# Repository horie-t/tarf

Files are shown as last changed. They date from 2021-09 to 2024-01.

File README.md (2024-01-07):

# Tarf

マイクロ・マウスを制作するプロジェクトです。

https://user-images.githubusercontent.com/10256609/150635355-fdfd84de-0ae6-4175-8a13-437b662bb9f7.mp4

Tarfは以下の特徴を持ちます。

* 筐体は3Dプリンタで制作
* 制御には、Wio Terminalを使用
* 制御用のFrimwareは、Rustで実装

## Rust開発環境のセットアップ

Ubuntu上で開発しています。

開発に必須のパッケージをインストールします。

```bash
sudo apt install build-essential git
```

Rustのツール・チェーンをインストールします。

[rustup](https://rustup.rs/) の指示に従ってインストールします。

クロスビルド用のツール・チェーンをインストールします。

```bash
rustup target add thumbv7em-none-eabihf
```

Wio Terminal用に必要なパッケージをインストールします。

```bash
sudo apt install libusb-1.0-0-dev libsdl2-dev libssl-dev
```

シリアルデバイスの読み書き権限の設定

```bash
sudo adduser $USER dialout
```

上記で、Wio Terminalにプログラムの書き込みができない場合は以下のファイルを作成します。

/etc/udev/rules.d/99-seeed-boards.rules
```
ATTRS{idVendor}=="2886", ENV{ID_MM_DEVICE_IGNORE}="1"
SUBSYSTEM=="usb", ATTRS{idVendor}=="2886", MODE="0666"
SUBSYSTEM=="tty", ATTRS{idVendor}=="2886", MODE="0666"
```

作成後、以下のコマンドを実行します。

```bash
sudo udevadm control --reload-rules
```

## 開発記録

Firmware

| ステップ | 内容 |
| --- | --- |
| 1 | [内蔵LEDでLチカ](./firmware/l-chika)をしてみる。 |
| 2 | ブレッドボードに接続して、[外部のLEDでLチカ](./firmware/l-chika-external)してみる。 | 
| 3 | L6470モータドライバを使って、[ステッピングモータを駆動](./firmware/stepper-motor)させてみる。|
| 4 | L6470モータドライバを使って、[ステッピングモータをステップ数指定で駆動](./firmware/stepper-motor-count)させてみる。|
| 5 | 外部の[スイッチからの割込み](./firmware/interrupt-external)を受け付ける。 |
| 6 | [ステッピングモータの動作完了を割込みで処理する](./firmware/stepper-motor-interrupt)。 |
| 7 | A4988モータドライバを使って、[ステッピングモータを駆動](./firmware/stepper-motor-a4988)させてみる。 |
| 8 | [3つのステッピングモータを駆動](./firmware/stepper-motor-a4988-3motor)させてみる。 |
| 9 | TimerContorllerの割込みを使って[3つのステッピングモータを別々の回転数で駆動](./firmware/stepper-motor-a4988-timer)させてみる。 |
| 10 | [試作1号機で往復運動](./firmware/reciprocating-motion)をさせてみる。 |
| 11 | [往復運動をタイマー割込み](./firmware/reciprocating-timer)でさせてみる。 |
| 12 | [三角形の軌跡](./firmware/triangle-motion)を描くように移動させる。 |
| 13 | 段々と速度を上げる[加速運動](./firmware/accelaration)をさせる。 |
| 14 | [TOF 距離センサ](./firmware/tof-sensor/)を接続する。 |
| 15 | [LCDに文字](./firmware/lcd-display/)を表示する。 |
| 16 | [TOF 距離センサを6つ](./firmware/tof-sensor-hub-6/)接続する。 |
| 17 | [TOF 距離センサで連続測定モード](./firmware/tof-sensor-interrupt/)で測定する。 |
| 18 | [2マスの直線だけの迷路](./firmware/straight-line-maze/)を走行する。 |
| 19 | [L字型迷路](./firmware/l-shaped-maze/)をデッド・レコニングで走行する。 |
| 20 | [長い直線迷路](./firmware/long-straight-maze/)を補正しながら走行する。 |
| 21 | [スタート位置で向きと位置を調整](./firmware/adjust-position/)してから走行する。 |
| 22 | [4マスの迷路](./firmware/quad-cell-maze/)を走行する。 |
| 23 | 9マスの[渦巻き状の迷路](./firmware/spiral-maze/)を走行する。 |
| 23 | 9マスの[迷路を描画](./firmware/map-display/)してみる。 |
| 23 | 9マスの渦巻き状の迷路を[現在地を表示](./firmware/current-pose/)しながら走行する。 |
| 24 | 9マスの渦巻き状の迷路を[側面の壁を表示](./firmware/wall-state/)しながら走行する。 |
| 25 | [BNO055 9軸センサ](./firmware/9axis-sensor/)を接続する。 |
| 26 | [UARTにHello, worldを出力](./firmware/uart/)する。 |
| 25 | [9軸センサをI2Cハブ](./firmware/9axis-sensor-hub/)に接続する。 |
| *** | 以降、設計見直し |
| 26 | [内蔵LEDでLチカ(その3)](./firmware/l-chika-3)をしてみる。 |

Body

| ステップ | 内容 |
| --- | --- |
| 1 | [ステッピングモータを固定](./cad/core1_3_motor) |
| 2 | [ステッピングモータを固定の向きを変更](./cad/core1_3_motor2) |
| 3 | [ステッピングモータとWio Terminal部分との接続部を追加](./cad/core1_3_motor3) |
| 4 | [Wio Terminalとバッテリーの収納部](./cad/core2) |
| 5 | [オムニホイールのハブを作成](./cad/wheel_hub) |
| 6 | [TOF距離センサを搭載](./cad/core1_motor_sensor_4) |
| 7 | [Wio Terminalとバッテリーの収納部にI2Cハブを搭載](./cad/core2_3) |
| *** | 以降大幅な設計変更 |
| 8 | [TOF距離センサの位置を変更](./cad/core1_motor_sensor_5/) |
| 9 | [Wio Terminalとバッテリーの格納部の下部の長さ調整](./cad/core2_5/) |

curcuit
| ステップ | 内容 |
| --- | --- |
| 1 | [回路図](./circuit/universal_board_both.svg)  |

## 参考情報

* embedded-halクレートの[RustDoc](https://docs.rs/embedded-hal/0.2.6/embedded_hal/)
* ATSAMDマイコンのRustクレートの[リポジトリ](https://github.com/atsamd-rs/atsamd)  
  Wio Terminalのクレートもこの中
* atsamd51pのRustクレートの[RustDoc](https://docs.rs/atsamd51p/0.9.0/atsamd51p/)
* wio_terminalクレートの[RustDoc](https://docs.rs/wio_terminal/0.3.0/wio_terminal/)

* VL53L0Xの[使い方](./docs/VL53L0X.md)

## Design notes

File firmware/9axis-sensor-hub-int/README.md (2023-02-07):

# 9軸センサーをI2Cハブ経由で接続し、割込みで測定する

2023-02-07: 上手く割込みが動作しない

## 使用パーツ

* [Wio Terminal](https://www.switch-science.com/catalog/6360/)
* [Wio Terminal バッテリーベース](https://www.switch-science.com/catalog/6816/)
* [ＢＮＯ０５５使用　９軸センサーフュージョンモジュールキット](https://akizukidenshi.com/catalog/g/gK-16996/)
* [Grove 8チャンネルI2Cマルチプレクサ/I2Cハブ(TCA9548A)](https://eleshop.jp/shop/g/gK2C313/)
* [USBシリアル変換モジュール(通販コード:M-11007)](https://akizukidenshi.com/catalog/g/gM-11007/)

## 測定値をパソコンで確認

Linuxの場合:

minicomをインストールして、以下のコマンドを実行します。

```bash
minicom -D /dev/ttyUSB0
```

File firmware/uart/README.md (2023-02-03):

# 9軸センサー

## 使用パーツ

* [Wio Terminal](https://www.switch-science.com/catalog/6360/)
* [USBシリアル変換モジュール(通販コード:M-11007)](https://akizukidenshi.com/catalog/g/gM-11007/)

## 測定値をパソコンで確認

Linuxの場合:

minicomをインストールして、以下のコマンドを実行します。

```bash
minicom -D /dev/ttyUSB0
```

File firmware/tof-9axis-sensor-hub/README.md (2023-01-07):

# 9軸センサー

## 使用パーツ

* [Wio Terminal](https://www.switch-science.com/catalog/6360/)
* [Wio Terminal バッテリーベース](https://www.switch-science.com/catalog/6816/)
* [ＢＮＯ０５５使用　９軸センサーフュージョンモジュールキット](https://akizukidenshi.com/catalog/g/gK-16996/)
* [USBシリアル変換モジュール(通販コード:M-11007)](https://akizukidenshi.com/catalog/g/gM-11007/)

## ブレッドボードで接続する場合の接続図

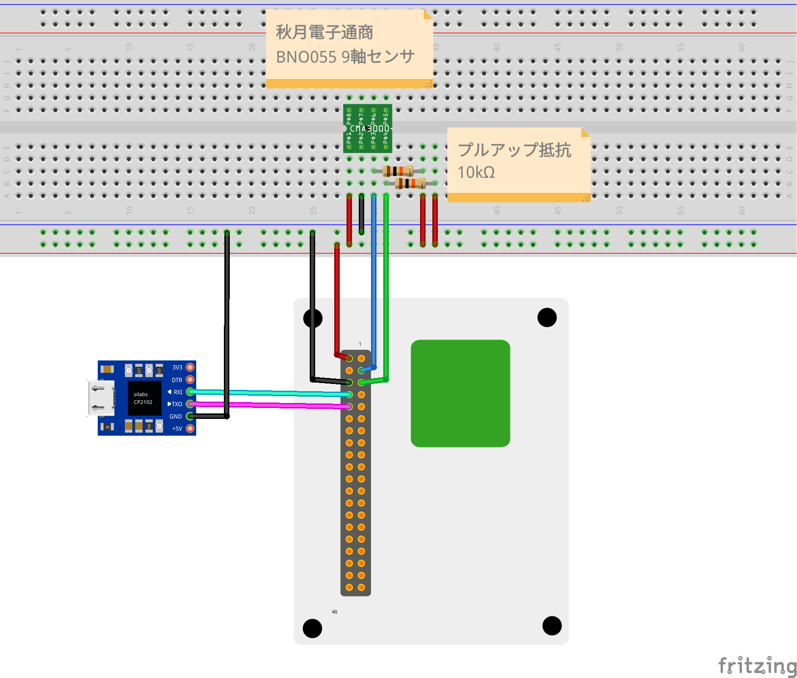
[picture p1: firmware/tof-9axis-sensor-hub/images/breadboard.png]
Breadboad


## 測定値をパソコンで確認

Linuxの場合:

minicomをインストールして、以下のコマンドを実行します。

```bash
minicom -D /dev/ttyUSB0
```

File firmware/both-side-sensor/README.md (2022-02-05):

# 両側のセンサの測定値で走行する

両側のセンサの値を使って走行する。できるだけ直進性を上げるのが目標。

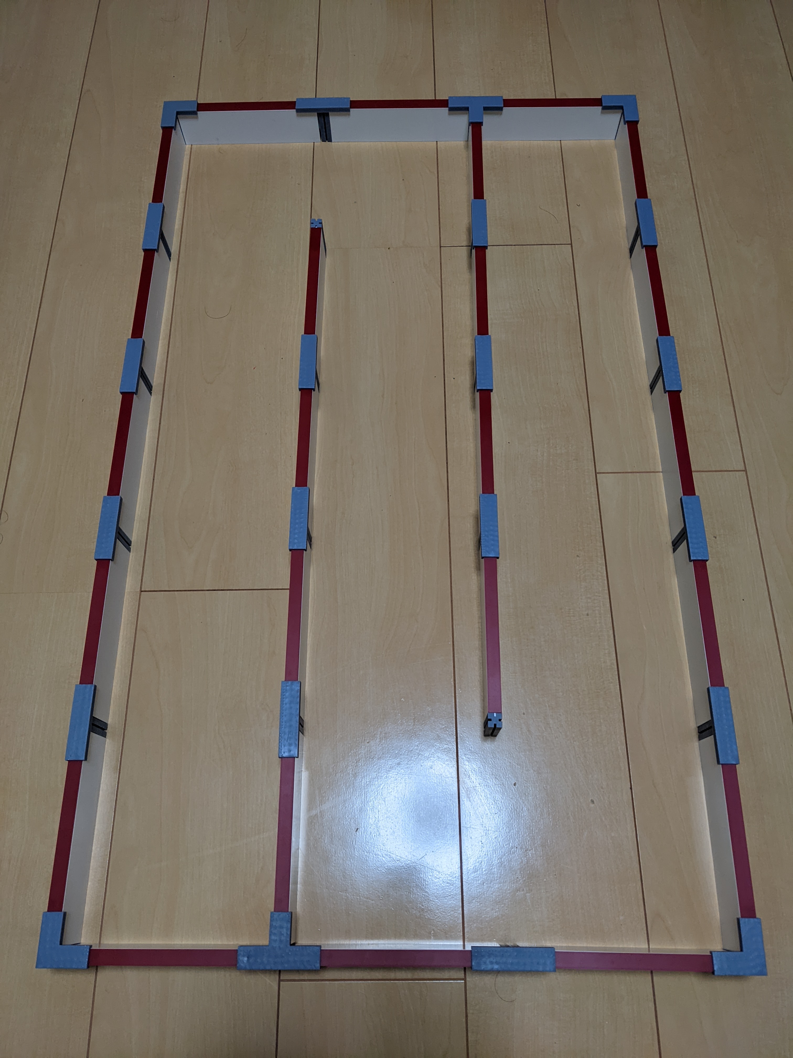
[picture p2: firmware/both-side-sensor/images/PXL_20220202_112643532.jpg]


## 使用パーツ

* [Wio Terminal](https://www.switch-science.com/catalog/6360/)
* [Wio Terminal バッテリーベース](https://www.switch-science.com/catalog/6816/)
* [バイポーラ・ステッピングモータ](https://jp.misumi-ec.com/vona2/detail/221005433134/?HissuCode=SS2421-5041)
* [A4988 ステッピングモータ・ドライバ・モジュール](https://amzn.to/39Z4EZu)
* [ToF レーザーモジュール(VL53L0X)](https://www.amazon.co.jp/gp/product/B08NDN4L9H/)
* [Grove 8チャンネルI2Cマルチプレクサ/I2Cハブ(TCA9548A)](https://eleshop.jp/shop/g/gK2C313/)
* [LiPoバッテリー](https://amzn.to/3DF7PCH)
* [クラシックサイズマイクロマウス迷路用 壁 (プラスチック)](https://www.rt-shop.jp/index.php?main_page=product_info&products_id=3745)

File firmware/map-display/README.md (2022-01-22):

# 地図描画

地図、ルートと自車位置を描画します。



## 使用パーツ

* [Wio Terminal](https://www.switch-science.com/catalog/6360/)

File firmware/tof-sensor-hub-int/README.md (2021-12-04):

# TOFセンサー

連続測定モードで測定

## 使用パーツ

* [Wio Terminal](https://www.switch-science.com/catalog/6360/)
* [Wio Terminal バッテリーベース](https://www.switch-science.com/catalog/6816/)
* [ToF レーザーモジュール(VL53L0X)](https://www.amazon.co.jp/gp/product/B08NDN4L9H/)
* [USBシリアル変換モジュール(通販コード:M-11007)](https://akizukidenshi.com/catalog/g/gM-11007/)

## ブレッドボードで接続する場合の接続図

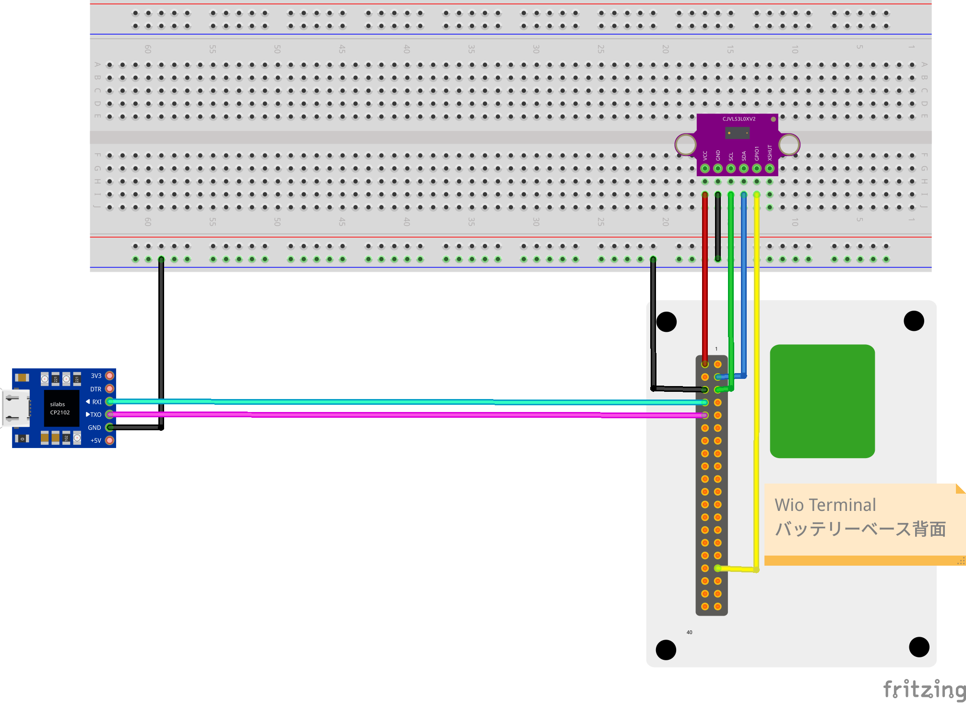
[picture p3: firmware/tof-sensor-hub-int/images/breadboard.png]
Breadboad


## 測定値をパソコンで確認

Linuxの場合:

minicomをインストールして、以下のコマンドを実行します。

```bash
minicom -D /dev/ttyUSB0
```

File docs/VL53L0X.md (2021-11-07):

# VL53L0Xの簡単な説明

## はじめに

VL53L0Xはレーザー光を利用したTOF型距離センサです。

最大測定距離は以下の通り。

| Target reflectance level(full FOV) | Conditions | Indoor(2)  | Outdoor overcast (2) |
| --- | --- | --- | --- |
| White target (88%) | Typical | 200cm+ (1) | 80cm |
| | Minimum | 120cm | 60cm |
| Grey target (17%) | Typical | 80cm | 50cm |
| | Minimum | 70cm | 40cm |

(VL53L0X Datasheet P.26より)

ホストとはI2Cで接続されます。I2Cバスの最大速度は400kbpsです。レジスタの仕様は公開されていない。

## 距離の測定

測定方法は以下の2つの方法です。

* ポーリングモード
* 割込みモード: 値が利用可能になると割込みピン(GPIO1)がホストに割込みを送信します。

## 測定シーケンス

ポーリングモードで測定する場合はAPI呼び出し後、timing buget(デフォルトは33msec) の時間以内で測定します。

## 測定プロファイル

| Range profile | Range timing budget | Typical performance | Typical application |
| --- | --- | --- | --- |
| Default mode  | 30 ms | 1.2 m, accuracy omit | Standard |
| High accuracy | 200 ms | 1.2 m, accuracy < +/- 3 % | Precise measurement |
| Long range | 33 ms | 2 m, accuracy omit | Long ranging, only for dark conditions  (no IR) |
| High speed | 20 ms | 1.2 m, accuracy +/- 5 % | High speed where accuracy is not priority |

(VL53L0X Datasheet P.28より)

timing budgetは、最小 20 ms, 最大 1000 ms。

## vl53l0xクレートの使用方法

Cargo.tomlの設定は [creates.io](https://crates.io/crates/vl53l0x) を参照。

**【インスタンスの生成】**
VL53L0x::new(i2c)

**【単発での測定】**

1. read_range_single_millimeters_blocking()

**【割込みでの連続測定】**

1. start_continuous(timing budgetのミリ秒)
2. 割込み発生
3. read_range_continuous_millimeters_blocking() もしくは read_range_mm()
4. 2, 3の繰り返し
5. (測定停止の場合)stop_continuous()

**【timing budget】**

get_measurement_timing_budget(ミリ秒)
set_measurement_timing_budget(ミリ秒)

使用例

* ポーリングモードの[例](../firmware/tof-sensor/src/main.rs)

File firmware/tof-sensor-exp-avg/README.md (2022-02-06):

# TOFセンサー

連続測定モードで測定し、指数平滑平均で表示する。

壁が直角



| 距離(mm) | センサ0 | センサ1 | センサ2 | センサ3 | センサ4 | センサ5 |
| --- | --- | --- | --- | --- | --- | --- |
| 10 | 28 | 17 | 14 | 22 | 20 | 38 |
| 20 | 33 | 24 | 23 | 24 | 25 | 41 |
| 30 | 49 | 37 | 37 | 37 | 36 | 53 |
| 40 | 59 | 47 | 48 | 42 | 49 | 62 |
| 50 | 68 | 56 | 55 | 51 | 55 | 68 |
| 60 | 76 | 66 | 65 | 59 | 67 | 80 |
| 70 | 88 | 77 | 74 | 73 | 76 | 92 |
| 80 | 98 | 88 | 87 | 82 | 87 | 102 |
| 90 | 109 | 97 | 96 | 93 | 96 | 112 |
| 100 | 118 | 106 | 105 | 104 | 105 | 123 |
| 120 | 138 | 130 | 129 | 122 | 127 | 141 |
| 140 | 161 | 151 | 149 | 146 | 148 | 164 |
| 160 | 179 | 169 | 170 | 161 | 168 | 184 |
| 180 | 198 | 187 | 189 | 186 | 186 | 202 |
| 200 | 217 | 208 | 209 | 206 | 205 | 220 |

壁が30°傾斜



| 距離(mm) | センサ0 | センサ1 | センサ2 | センサ3 | センサ4 | センサ5 |
| --- | --- | --- | --- | --- | --- | --- |
| 10 | 35 | 35 | 29 | 32 | 31 | 45 |
| 20 | 45 | 39 | 35 | 38 | 37 | 51 |
| 30 | 57 | 49 | 49 | 44 | 51 | 57 |
| 40 | 63 | 56 | 52 | 53 | 57 | 63 |
| 50 | 74 | 68 | 65 | 64 | 66 | 75 |
| 60 | 85 | 80 | 76 | 75 | 76 | 86 |
| 70 | 96 | 90 | 86 | 84 | 87 | 97 |
| 80 | 107 | 101 | 96 | 96 | 98 | 109 |
| 90 | 118 | 112 | 107 | 108 | 107 | 119 |
| 100 | 128 | 123 | 118 | 119 | 117 | 131 |
| 120 | 148 | 142 | 139 | 140 | 138 | 153 |
| 140 | 167 | 162 | 158 | 161 | 157 | 172 |
| 160 | 187 | 179 | 178 | 181 | 176 | 191 |
| 180 | 206 | 197 | 196 | 200 | 196 | 212 |
| 200 | 223 | 215 | 214 | 219 | 215 | 231 |

## 使用パーツ

* [Wio Terminal](https://www.switch-science.com/catalog/6360/)
* [Wio Terminal バッテリーベース](https://www.switch-science.com/catalog/6816/)
* [ToF レーザーモジュール(VL53L0X)](https://www.amazon.co.jp/gp/product/B08NDN4L9H/)
* [Grove 8チャンネルI2Cマルチプレクサ/I2Cハブ(TCA9548A)](https://eleshop.jp/shop/g/gK2C313/)
* [USBシリアル変換モジュール(通販コード:M-11007)](https://akizukidenshi.com/catalog/g/gM-11007/)

## ブレッドボードで接続する場合の接続図

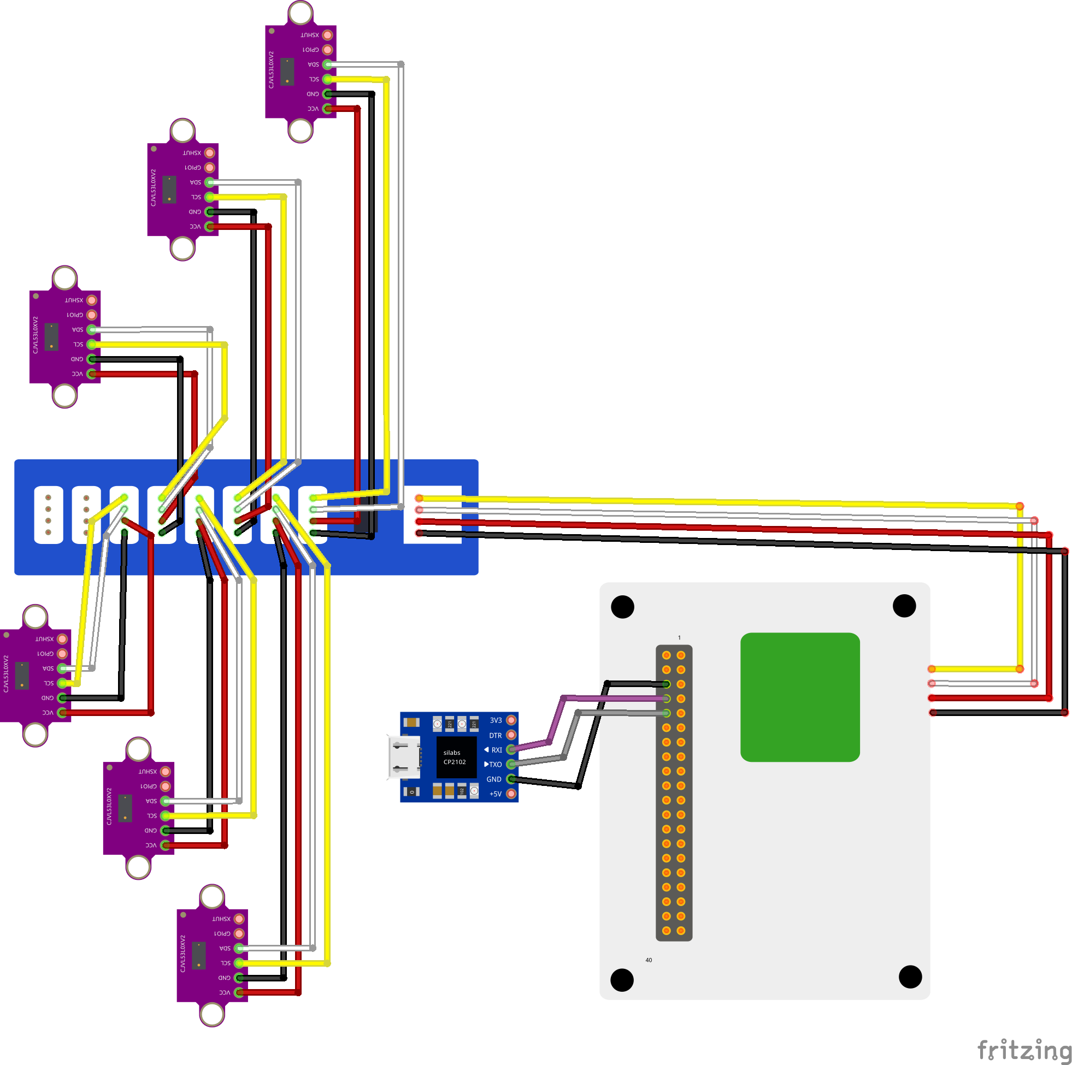
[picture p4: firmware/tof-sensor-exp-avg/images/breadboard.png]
Breadboad


## 測定値をパソコンで確認

Linuxの場合:

minicomをインストールして、以下のコマンドを実行します。

```bash
minicom -D /dev/ttyUSB0
```

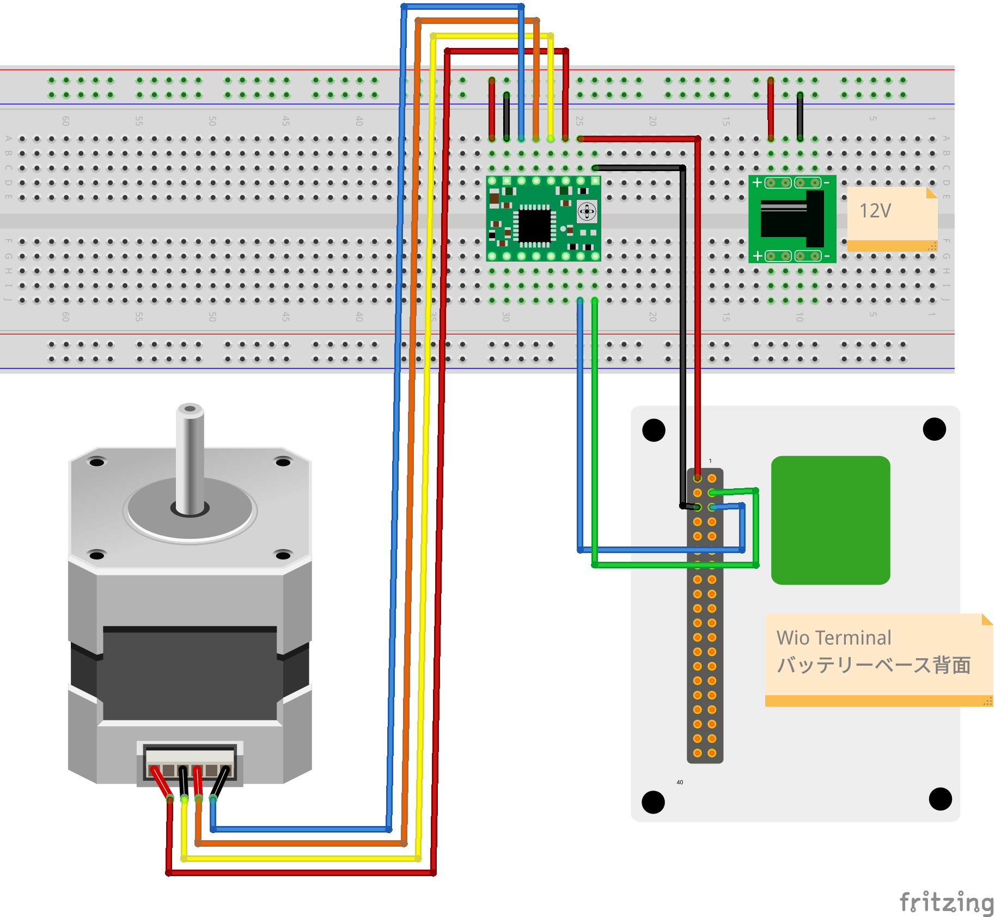
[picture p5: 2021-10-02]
firmware/stepper-motor-a4988/images/stepper_motor_breadboard.png

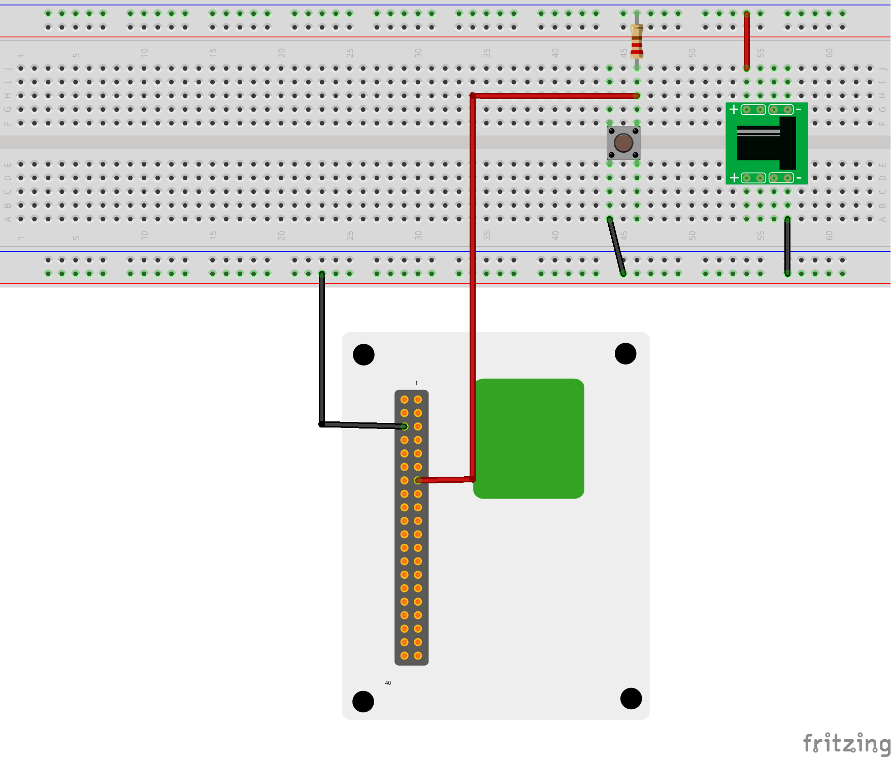
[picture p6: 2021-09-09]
firmware/interrupt-external/images/button_external.png

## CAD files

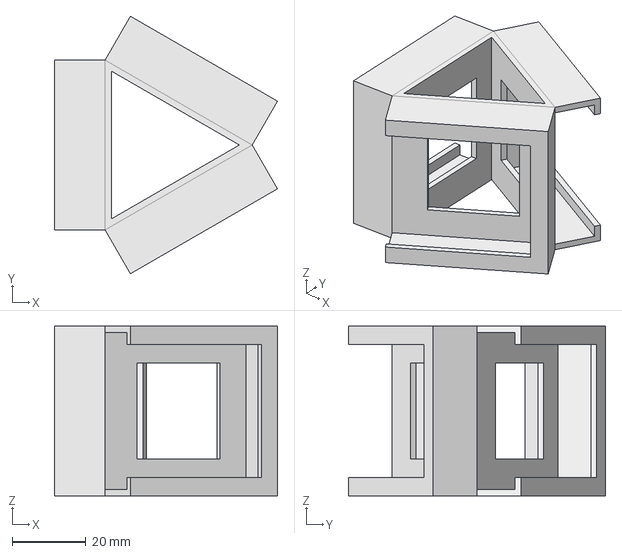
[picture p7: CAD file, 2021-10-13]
cad/core1_3_motor/core1_3_motor.FCStd
60.4 x 69.7 x 46.0 mm

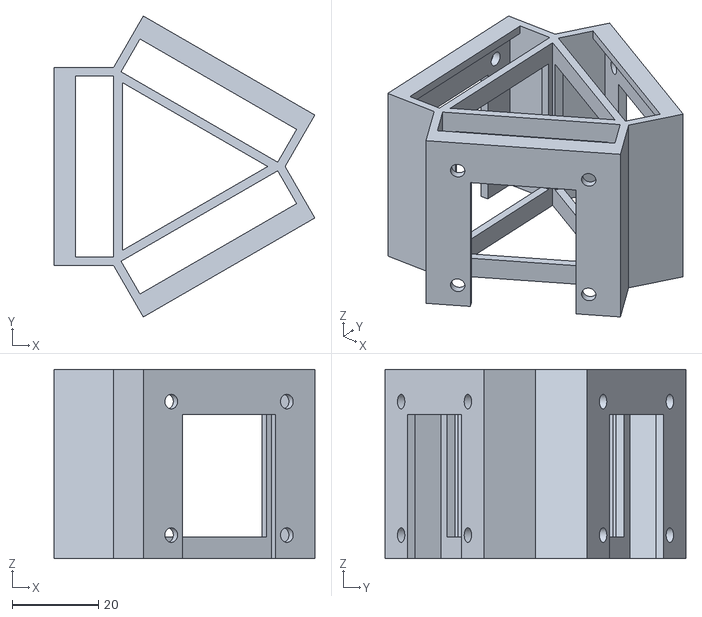
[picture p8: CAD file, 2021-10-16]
cad/core1_3_motor_2/core1_3_motor_2-Body.stl
60.5 x 69.9 x 44.0

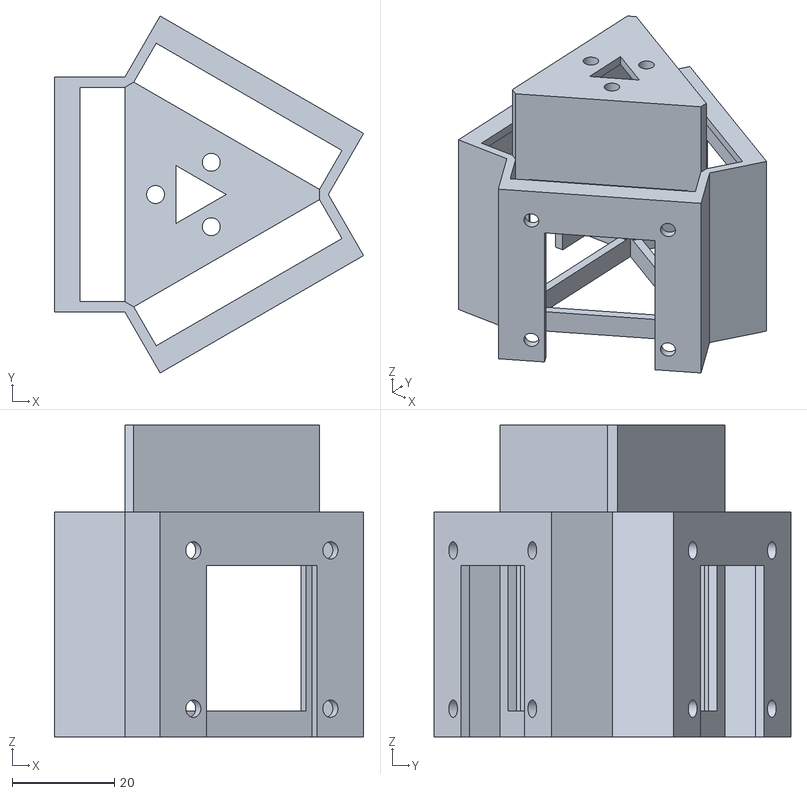
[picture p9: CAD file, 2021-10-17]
cad/core1_3_motor_3/core1_3_motor_3-Body.stl
60.5 x 69.9 x 61.0

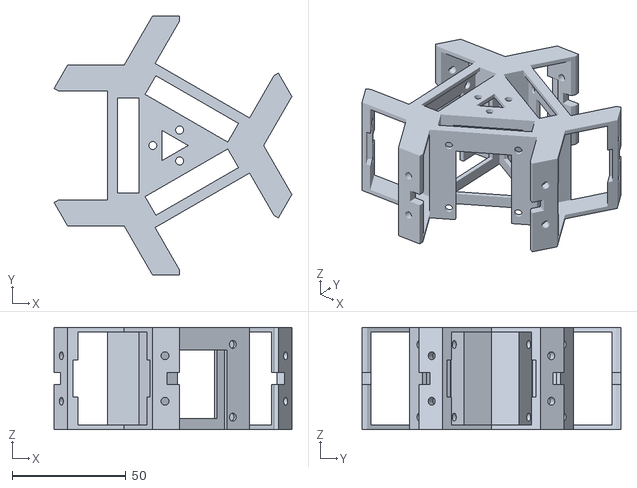
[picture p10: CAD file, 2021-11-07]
cad/core1_motor_sensor/core1_motor_sensor-Body.stl
104.7 x 114.0 x 45.0

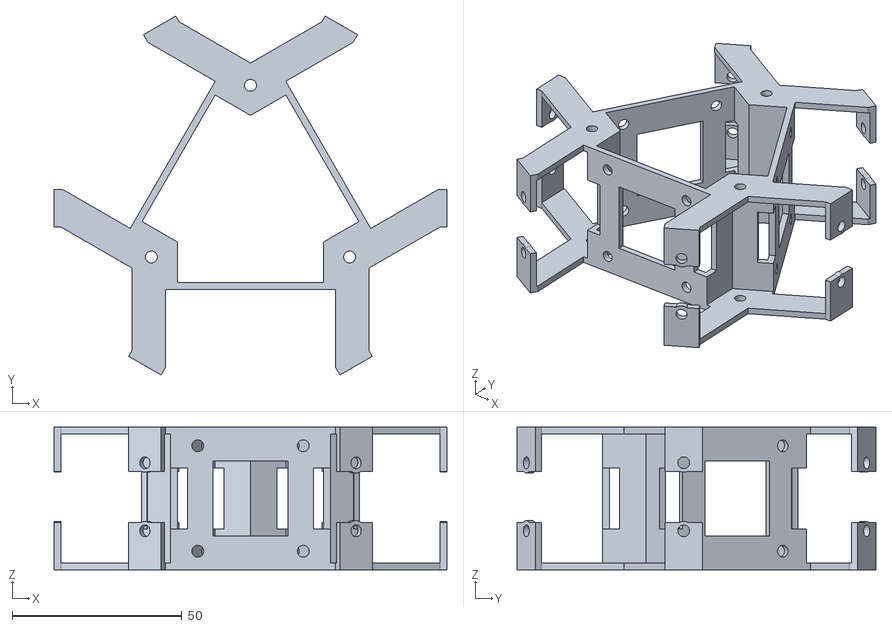
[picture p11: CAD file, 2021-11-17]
cad/core1_motor_sensor_2/core1_motor_sensor_2-Body.stl
115.6 x 105.6 x 42.0

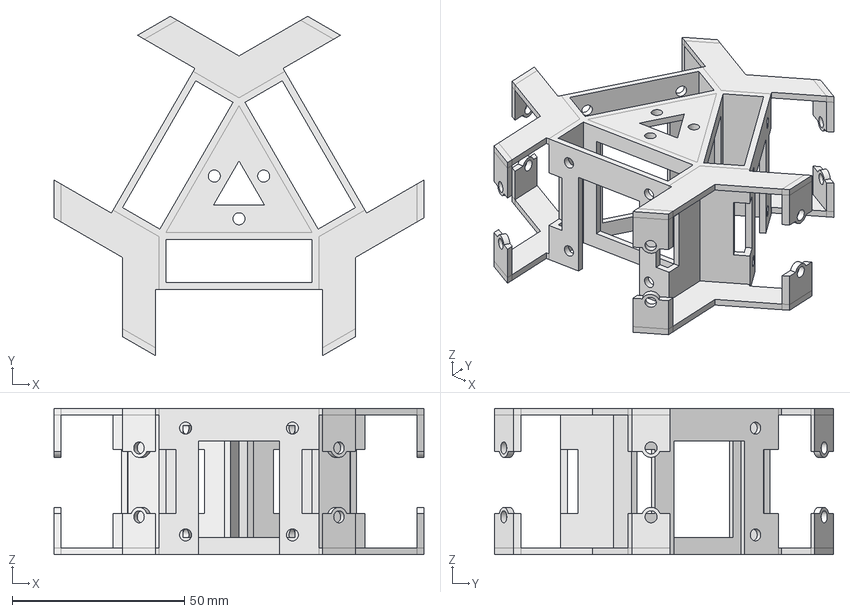
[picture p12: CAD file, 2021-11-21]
cad/core1_motor_sensor_4/core1_motor_sensor_4.FCStd
107.4 x 98.5 x 42.5 mm

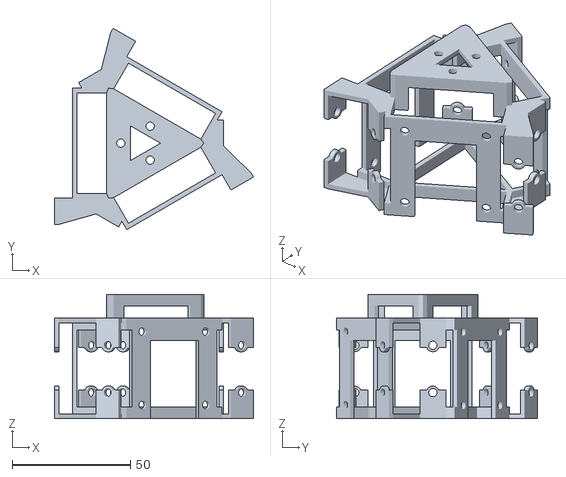
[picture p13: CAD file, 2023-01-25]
cad/core1_motor_sensor_5/core1_motor_sensor_5-Body.stl
84.1 x 85.1 x 52.5

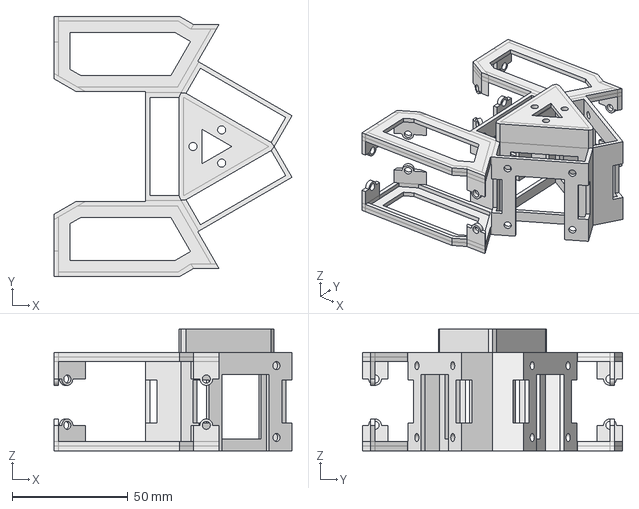
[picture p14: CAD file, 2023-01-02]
cad/core1_motor_tof_9axis/core1_motor_tof_9axis.FCStd
102.8 x 112.5 x 52.5 mm

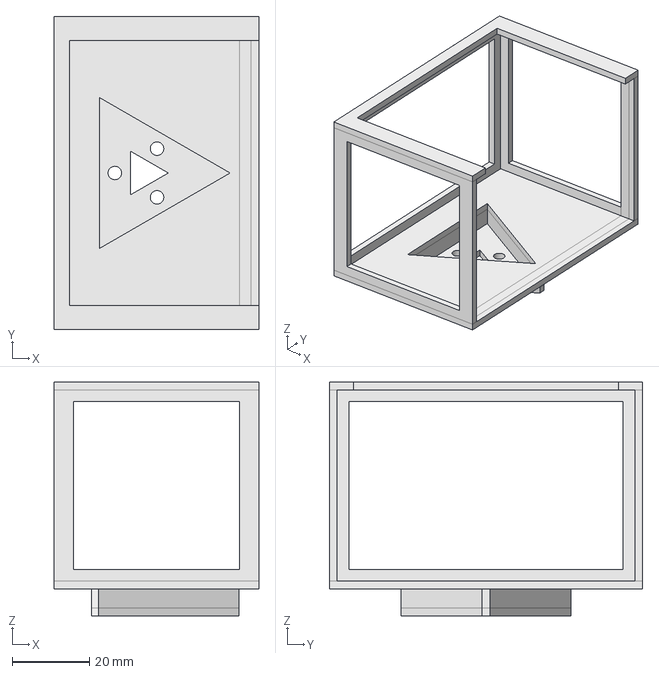
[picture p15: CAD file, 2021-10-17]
cad/core2/core2.FCStd
53.0 x 81.0 x 60.5 mm

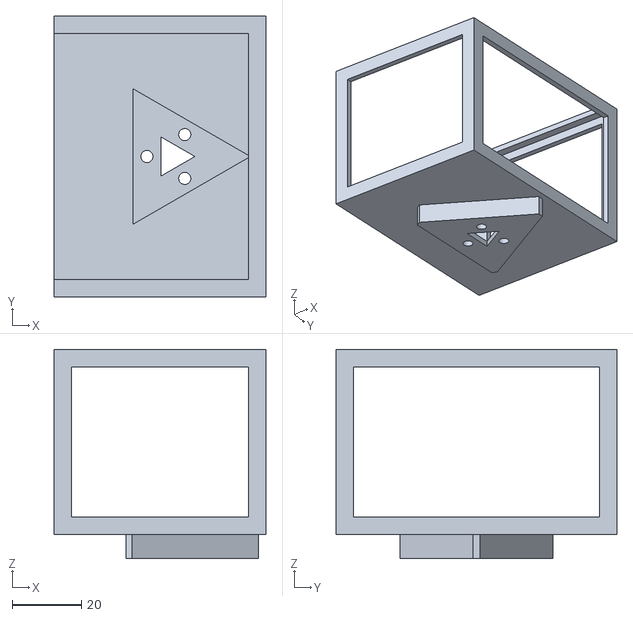
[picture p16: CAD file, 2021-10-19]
cad/core2_2/core2_2-Body.stl
61.0 x 81.0 x 60.3

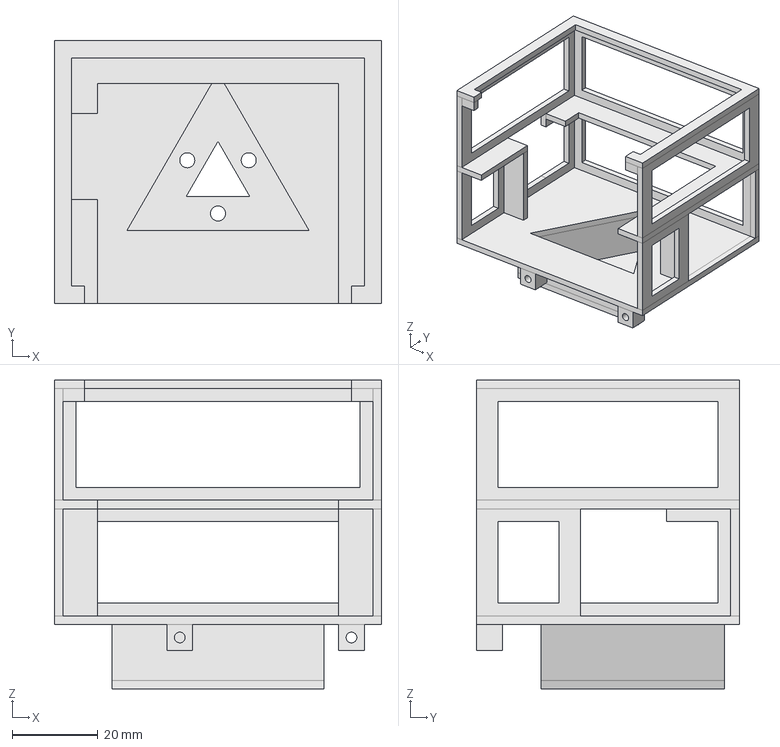
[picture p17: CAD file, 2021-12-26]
cad/core2_3/core2_3.FCStd
76.2 x 61.2 x 72.0 mm

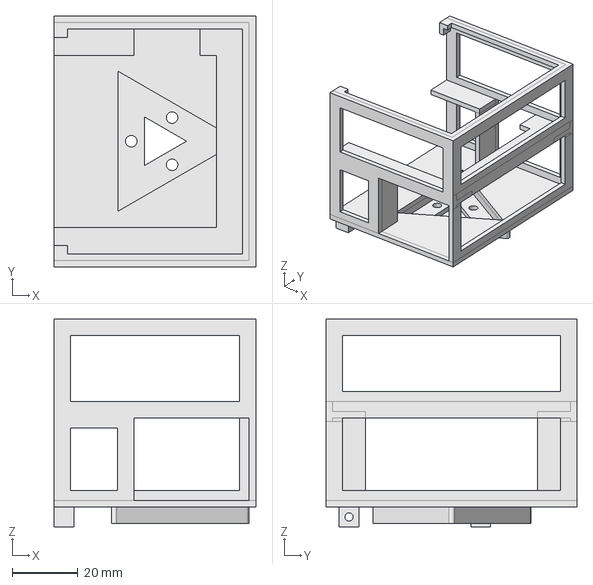
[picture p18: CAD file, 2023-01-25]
cad/core2_4/core2_4.FCStd
61.2 x 76.2 x 63.0 mm

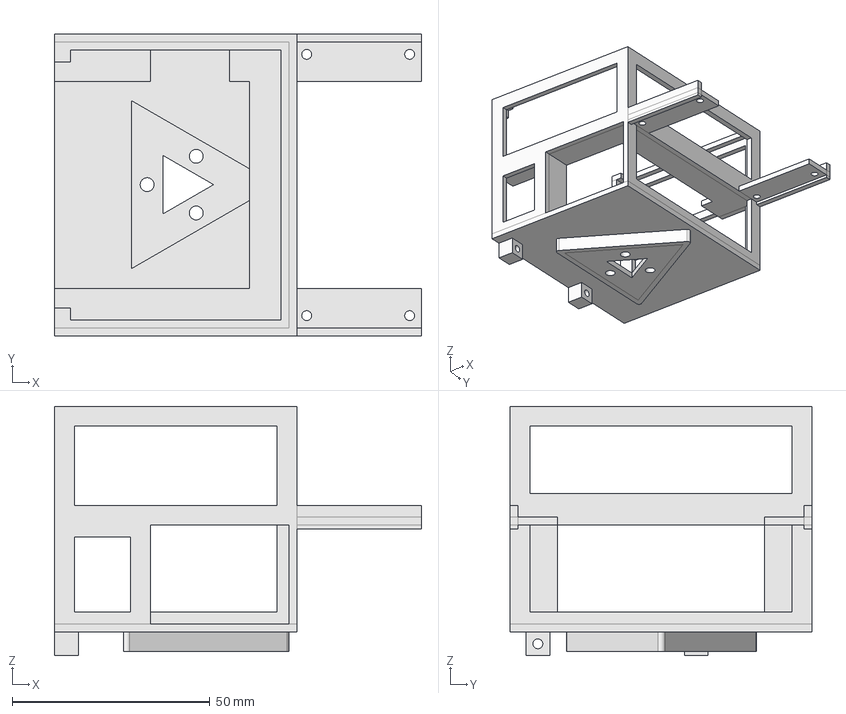
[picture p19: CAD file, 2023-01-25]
cad/core2_9axis/core2_9axis.FCStd
92.7 x 76.2 x 63.0 mm

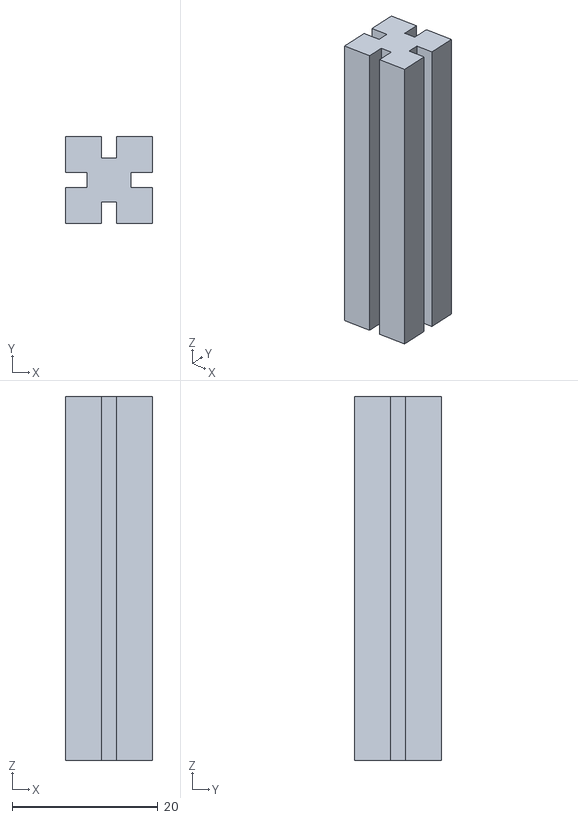
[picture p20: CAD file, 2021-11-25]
cad/maze_pillar/maze_pillar-Body.stl
12.0 x 12.0 x 50.0

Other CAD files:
cad/core1_motor_sensor_3/core1_motor_sensor_3.FCStd
cad/core2_5/core2_5.FCStd
cad/maze_wall_cap/maze_wall_cap-Body.stl
cad/maze_wall_cap_I/maze_wall_cap_I.FCStd
cad/core1_3_motor/core1_3_motor-Body.stl
cad/core1_3_motor_2/core1_3_motor_2.FCStd
cad/core1_3_motor_3/core1_3_motor_3.FCStd
cad/core1_motor_sensor/core1_motor_sensor.FCStd
cad/core1_motor_sensor_2/core1_motor_sensor_2.FCStd
cad/core1_motor_sensor_3/core1_motor_sensor_3-Body.stl
cad/core1_motor_sensor_4/core1_motor_sensor_4-Body.stl
cad/core1_motor_sensor_5/core1_motor_sensor_5.FCStd
cad/core1_motor_tof_9axis/core1_motor_tof_9axis-Body.stl
cad/core2/core2-Body.stl
cad/core2_2/core2_2.FCStd
cad/core2_3/core2_3-Body.stl
cad/core2_4/core2_4-Body.stl
cad/core2_5/core2_5-Body.stl
cad/core2_9axis/core2_9axis-Body.stl
cad/maze_pillar/maze_pillar.FCStd
cad/maze_wall_cap/maze_wall_cap.FCStd
cad/maze_wall_cap_I/maze_wall_cap_I-Body.stl
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

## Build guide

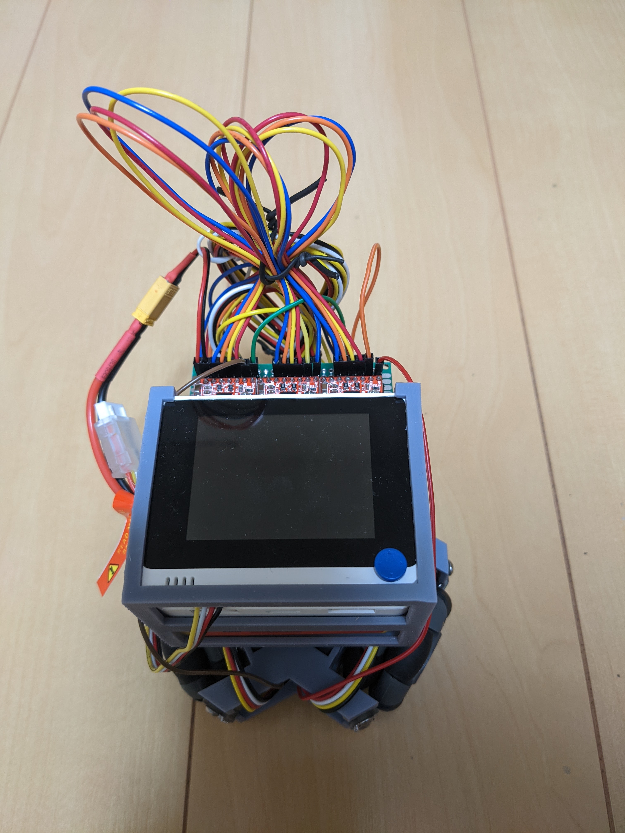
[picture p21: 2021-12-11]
assembly/PXL_20211211_084058963.jpg

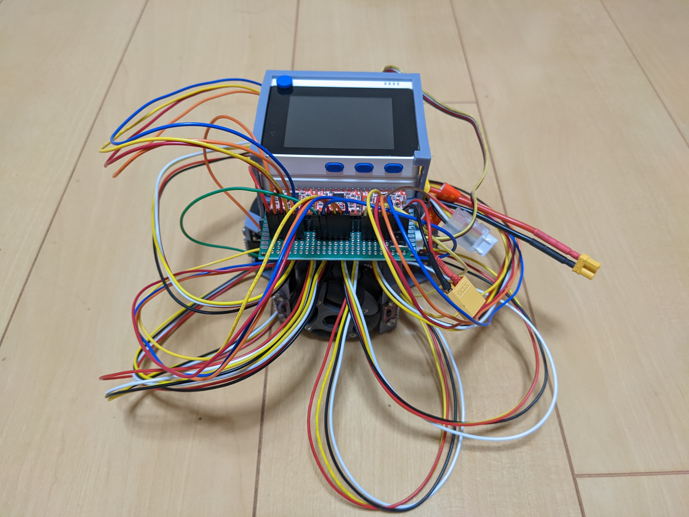
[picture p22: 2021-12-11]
assembly/PXL_20211209_231504273.jpg

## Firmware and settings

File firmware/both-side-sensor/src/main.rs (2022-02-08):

#![no_std]
#![no_main]

use core::f32::consts::{PI, FRAC_PI_2, FRAC_PI_3, FRAC_PI_4, FRAC_PI_6, FRAC_PI_8};
use core::fmt::Write;
use core::iter::FromIterator;

use cortex_m::interrupt::free as disable_interrupts;
use heapless::String;
use heapless::Vec;
use heapless::consts::*;
use heapless::spsc::Queue;
use micromath::F32Ext;
use vl53l0x::VL53L0x;
use xca9548a::{SlaveAddr, Xca9548a};

use panic_halt as _;

use embedded_graphics::prelude::*;

use nalgebra as na;
use na::{Vector3, matrix, vector, Matrix3, Vector2};

use wio_terminal as wio;
use wio::{entry, Display, Pins};
use wio::hal::clock::GenericClockController;
use wio::hal::delay::Delay;
use wio::hal::common::eic;
use wio::hal::gpio::v1::{Pa16, Pa17, PfD};
use wio::hal::gpio::v2::{PA07, PB04, PB05, PB06, PB08, PB09};
use wio::hal::sercom::{I2CMaster3, PadPin, Sercom3Pad0, Sercom3Pad1};
use wio::hal::timer::TimerCounter;
use wio::pac::{CorePeripherals, Peripherals, TC2, TC3, TC4, interrupt};
use wio::prelude::*;

mod console;
use console::{Button, ButtonEvent, MapView, clear_display, println_display, print_current_cell, print_current_pose, SideWallView};

mod runningsystem;
use runningsystem::{RunningSystem, Wheel, WheelMovedEvent, WheelRotateDirection};

mod sensor;
use sensor::{SensorEvent, SensorI2C, TofSensors, SensorMeasuredValue};

mod maze;
use maze::{Maze, calc_side_wall};
use maze::{CELL_____, CELL_N___, CELL__E__, CELL_NE__, CELL___S_, CELL_N_S_, CELL__ES_, CELL_NES_, CELL____W, CELL_N__W, CELL__E_W, CELL_NE_W, CELL___SW, CELL_N_SW, CELL__ESW, CELL_NESW, };
use maze::{NO_WALL, WALL, UNKNOWN_WALL};

static mut WHEEL_MOVED_EVENT_QUEUE: Queue<WheelMovedEvent, U16> = Queue(heapless::i::Queue::new());
static mut RUNNING_SYSTEM: Option<RunningSystem<PB08, PB09, TC2, PA07, PB04, TC3, PB05, PB06, TC4>> = None;

static mut START_BUTTON: Option<Button> = None;
static mut I2C_SWITCH: Option<Xca9548a<SensorI2C>> = None;
static mut TOF_SENSORS: Option<TofSensors> = None;
static mut EVENT_QUEUE: Queue<SensorEvent, U16> = Queue(heapless::i::Queue::new());

enum VehicleState {
    Idle,
    AdjustDir,
    AdjustCenter,
    Run,
    Turn,
    AdjustTrun,
    Arrive,
}

#[entry]
fn main() -> ! {
    // 初期化処理
    let mut peripherals = Peripherals::take().unwrap();
    let mut core = CorePeripherals::take().unwrap();
    let mut clocks = GenericClockController::with_external_32kosc(
        peripherals.GCLK,
        &mut peripherals.MCLK,
        &mut peripherals.OSC32KCTRL,
        &mut peripherals.OSCCTRL,
        &mut peripherals.NVMCTRL,
    );
    let mut delay = Delay::new(core.SYST, &mut clocks);

    let gclk0 = &clocks.gclk0();
    let gclk1 = clocks.gclk1();
    let gclk5 = clocks.get_gclk(wio::pac::gclk::pchctrl::GEN_A::GCLK5).unwrap();
    let tc2_tc3 = clocks.tc2_tc3(&gclk5).unwrap();
    let tc4_tc5 = clocks.tc4_tc5(&gclk5).unwrap();

    let mut configurable_eic = eic::init_with_ulp32k(&mut peripherals.MCLK, clocks.eic(&gclk1).unwrap(), peripherals.EIC);
    let nvic = &mut core.NVIC;

    let mut pins = Pins::new(peripherals.PORT);
    
    // 走行装置の初期化
    let wheel_mat = matrix![
        - 3.0_f32.sqrt() / 2.0_f32, - 0.5_f32, 49.0_f32;
          0.0_f32,                    1.0_f32, 49.0_f32;
          3.0_f32.sqrt() / 2.0_f32, - 0.5_f32, 49.0_f32;
    ];
    let running_system = RunningSystem {
        wheel_0: Wheel::new(0, pins.a0_d0.into(), pins.a1_d1.into(),
            TimerCounter::tc2_(&tc2_tc3, peripherals.TC2, &mut peripherals.MCLK), interrupt::TC2),
        wheel_1: Wheel::new(1, pins.a2_d2.into(), pins.a3_d3.into(),
            TimerCounter::tc3_(&tc2_tc3, peripherals.TC3, &mut peripherals.MCLK), interrupt::TC3),
        wheel_2: Wheel::new(2, pins.a4_d4.into(), pins.a5_d5.into(),
            TimerCounter::tc4_(&tc4_tc5, peripherals.TC4, &mut peripherals.MCLK), interrupt::TC4),
        mat_for_wheel_v: wheel_mat,
        mat_for_odometry: wheel_mat.try_inverse().unwrap(),
        velocity: Vector3::zeros(),
        target_point: Vector3::repeat(f32::MAX),
        trip_vec: Vector3::zeros(),
    };

    unsafe { RUNNING_SYSTEM = Some(running_system); }
    wheel_interrupt!(RUNNING_SYSTEM, TC2, wheel_0);
    wheel_interrupt!(RUNNING_SYSTEM, TC3, wheel_1);
    wheel_interrupt!(RUNNING_SYSTEM, TC4, wheel_2);

    let mut wheel_event_queue = unsafe { WHEEL_MOVED_EVENT_QUEUE.split().1 };

    // スタートボタンの初期化
    let start_button = Button::new(
        pins.button1,
        Queue::new(),
        &mut configurable_eic,
        &mut pins.port,
    );
    disable_interrupts(|_| {
        start_button.enable(nvic, interrupt::EIC_EXTINT_10);
    });
    unsafe { START_BUTTON = Some(start_button); }
    button_interrupt!(START_BUTTON, EIC_EXTINT_10);
    let mut start_event_queue = unsafe { START_BUTTON.as_mut().unwrap().queue.split().1 };

    // LCDの初期化
    let (mut display, _blacklight) = (Display {
        miso: pins.lcd_miso,
        mosi: pins.lcd_mosi,
        sck: pins.lcd_sck,
        cs: pins.lcd_cs,
        dc: pins.lcd_dc,
        reset: pins.lcd_reset,
        backlight: pins.lcd_backlight
    }).init(&mut clocks, peripherals.SERCOM7, &mut peripherals.MCLK, &mut pins.port, 58.mhz(), &mut delay)
    .ok().unwrap();
    clear_display(&mut display);

    // センサの初期化
    let i2c: I2CMaster3<Sercom3Pad0<Pa17<PfD>>, Sercom3Pad1<Pa16<PfD>>> = I2CMaster3::new(
        &clocks.sercom3_core(&gclk0).unwrap(),
        400.khz(),
        peripherals.SERCOM3,
        &mut peripherals.MCLK,
        pins.i2c1_sda.into_pad(&mut pins.port),
        pins.i2c1_scl.into_pad(&mut pins.port),
    );
    let i2c_switch = Xca9548a::new(i2c, SlaveAddr::default());
    unsafe {
        I2C_SWITCH = Some(i2c_switch);
        let i2c_ports = I2C_SWITCH.as_mut().unwrap().split();
        let tof_sensors = TofSensors::new(
            pins.a6_d6,
            VL53L0x::new(i2c_ports.i2c0).unwrap(),
            pins.a7_d7,
            VL53L0x::new(i2c_ports.i2c1).unwrap(),
            pins.a8_d8,
            VL53L0x::new(i2c_ports.i2c2).unwrap(),
            pins.gpclk0,
            VL53L0x::new(i2c_ports.i2c3).unwrap(),
            pins.gpclk1,
            VL53L0x::new(i2c_ports.i2c4).unwrap(),
            pins.gpclk2,
            VL53L0x::new(i2c_ports.i2c5).unwrap(),
            &mut configurable_eic,
            &mut pins.port,
        );
        disable_interrupts(|_| {
            tof_sensors.enable(nvic, interrupt::EIC_EXTINT_4, interrupt::EIC_EXTINT_7, interrupt::EIC_EXTINT_6,
                interrupt::EIC_EXTINT_14, interrupt::EIC_EXTINT_12, interrupt::EIC_EXTINT_13);
        });
        TOF_SENSORS = Some(tof_sensors);
    }
    tof_interrupt!(TOF_SENSORS, sensor0_gpio1, sensor0_i2c, 0u16, EIC_EXTINT_4);
    tof_interrupt!(TOF_SENSORS, sensor1_gpio1, sensor1_i2c, 1u16, EIC_EXTINT_7);
    tof_interrupt!(TOF_SENSORS, sensor2_gpio1, sensor2_i2c, 2u16, EIC_EXTINT_6);
    tof_interrupt!(TOF_SENSORS, sensor3_gpio1, sensor3_i2c, 3u16, EIC_EXTINT_14);
    tof_interrupt!(TOF_SENSORS, sensor4_gpio1, sensor4_i2c, 4u16, EIC_EXTINT_12);
    tof_interrupt!(TOF_SENSORS, sensor5_gpio1, sensor5_i2c, 5u16, EIC_EXTINT_13);
    let mut consumer = unsafe { EVENT_QUEUE.split().1 };
    let mut distances = [
        SensorMeasuredValue::new(0, -17.2_f32, -25.5_f32),
        SensorMeasuredValue::new(1, -5.9_f32, -21.2_f32),
        SensorMeasuredValue::new(2, -4.1_f32, 16.5_f32),
        SensorMeasuredValue::new(3, -4.2_f32, 15.3_f32),
        SensorMeasuredValue::new(4, -7.13_f32, 18.8_f32),
        SensorMeasuredValue::new(5, -22.6_f32, 27.6_f32),
    ];

    // 迷路の初期化(探索してないけどマッピングは終了していることにする)
    // 定義は左上を起点にしている
    let mut maze = Maze::from_iter(
        //探索・走行時は、迷路は左下を起点(maze[0][0])にして扱いたいので、revする。
        [
            Vec::from_iter([CELL_____, CELL_____, CELL_____, CELL_____, CELL_____, CELL_____, CELL_____, CELL_____, CELL_____, CELL_____, CELL_____, CELL_____, CELL_____, CELL_____, CELL_____, CELL_____].iter().cloned()),
            Vec::from_iter([CELL_____, CELL_____, CELL_____, CELL_____, CELL_____, CELL_____, CELL_____, CELL_____, CELL_____, CELL_____, CELL_____, CELL_____, CELL_____, CELL_____, CELL_____, CELL_____].iter().cloned()),
            Vec::from_iter([CELL_____, CELL_____, CELL_____, CELL_____, CELL_____, CELL_____, CELL_____, CELL_____, CELL_____, CELL_____, CELL_____, CELL_____, CELL_____, CELL_____, CELL_____, CELL_____].iter().cloned()),
            Vec::from_iter([CELL_____, CELL_____, CELL_____, CELL_____, CELL_____, CELL_____, CELL_____, CELL_____, CELL_____, CELL_____, CELL_____, CELL_____, CELL_____, CELL_____, CELL_____, CELL_____].iter().cloned()),
            Vec::from_iter([CELL_____, CELL_____, CELL_____, CELL_____, CELL_____, CELL_____, CELL_____, CELL_____, CELL_____, CELL_____, CELL_____, CELL_____, CELL_____, CELL_____, CELL_____, CELL_____].iter().cloned()),
            Vec::from_iter([CELL_____, CELL_____, CELL_____, CELL_____, CELL_____, CELL_____, CELL_____, CELL_____, CELL_____, CELL_____, CELL_____, CELL_____, CELL_____, CELL_____, CELL_____, CELL_____].iter().cloned()),
            Vec::from_iter([CELL_____, CELL_____, CELL_____, CELL_____, CELL_____, CELL_____, CELL_____, CELL_____, CELL_____, CELL_____, CELL_____, CELL_____, CELL_____, CELL_____, CELL_____, CELL_____].iter().cloned()),
            Vec::from_iter([CELL_____, CELL_____, CELL_____, CELL_____, CELL_____, CELL_____, CELL_____, CELL_____, CELL_____, CELL_____, CELL_____, CELL_____, CELL_____, CELL_____, CELL_____, CELL_____].iter().cloned()),
            Vec::from_iter([CELL_____, CELL_____, CELL_____, CELL_____, CELL_____, CELL_____, CELL_____, CELL_____, CELL_____, CELL_____, CELL_____, CELL_____, CELL_____, CELL_____, CELL_____, CELL_____].iter().cloned()),
            Vec::from_iter([CELL_____, CELL_____, CELL_____, CELL_____, CELL_____, CELL_____, CELL_____, CELL_____, CELL_____, CELL_____, CELL_____, CELL_____, CELL_____, CELL_____, CELL_____, CELL_____].iter().cloned()),
            Vec::from_iter([CELL_____, CELL_____, CELL_____, CELL_____, CELL_____, CELL_____, CELL_____, CELL_____, CELL_____, CELL_____, CELL_____, CELL_____, CELL_____, CELL_____, CELL_____, CELL_____].iter().cloned()),
            Vec::from_iter([CELL_N__W, CELL_NE__, CELL_NE_W, CELL_____, CELL_____, CELL_____, CELL_____, CELL_____, CELL_____, CELL_____, CELL_____, CELL_____, CELL_____, CELL_____, CELL_____, CELL_____].iter().cloned()),
            Vec::from_iter([CELL__E_W, CELL__E_W, CELL__E_W, CELL_____, CELL_____, CELL_____, CELL_____, CELL_____, CELL_____, CELL_____, CELL_____, CELL_____, CELL_____, CELL_____, CELL_____, CELL_____].iter().cloned()),
            Vec::from_iter([CELL__E_W, CELL__E_W, CELL__E_W, CELL_____, CELL_____, CELL_____, CELL_____, CELL_____, CELL_____, CELL_____, CELL_____, CELL_____, CELL_____, CELL_____, CELL_____, CELL_____].iter().cloned()),
            Vec::from_iter([CELL__E_W, CELL__E_W, CELL__E_W, CELL_____, CELL_____, CELL_____, CELL_____, CELL_____, CELL_____, CELL_____, CELL_____, CELL_____, CELL_____, CELL_____, CELL_____, CELL_____].iter().cloned()),
            Vec::from_iter([CELL__ESW, CELL___SW, CELL__ES_, CELL_____, CELL_____, CELL_____, CELL_____, CELL_____, CELL_____, CELL_____, CELL_____, CELL_____, CELL_____, CELL_____, CELL_____, CELL_____].iter().cloned()),
        ]
        .iter().rev().cloned()
    );

    // ルートの初期化
    // 左下を原点とする。
    let route = [
        (vector![0.0_f32, 0.0_f32], vector![0.0_f32, 4.0_f32]),
        (vector![0.0_f32, 4.0_f32], vector![1.0_f32, 4.0_f32]),
        (vector![1.0_f32, 4.0_f32], vector![1.0_f32, 0.0_f32]),
        (vector![1.0_f32, 0.0_f32], vector![2.0_f32, 0.0_f32]),
        (vector![2.0_f32, 0.0_f32], vector![2.0_f32, 4.0_f32])
        ];
    // スタート時点のリンクは0番目
    let mut link_index = 0;

    // 地図のViewの初期化
    let map_view = MapView {
        top_left: Point::new(150, 50),
        size: Size::new(161, 161)
    };
    map_view.draw_maze(&mut display, &mut maze);
    map_view.draw_route(&mut display, &route);

    let side_wall_view = SideWallView {
        top_left: Point::new(20, 80),
        size: Size::new(11, 11)
    };

    // 初期化の後処理
    configurable_eic.finalize();

    let mut vehicle_pose = vector![90.0_f32, 90.0_f32, 0.0_f32];
    let mut vehicle_state = VehicleState::Idle;
    let velocity = 50.0_f32;

    let mut moved_count = 0_u64;
    let mut drawed_moved_count = 0_u64; // FIXME: きれいな実装ではない。
    map_view.draw_vehicle(&mut display, &vehicle_pose);

    println_display(&mut display, "Initialiezed");

    loop {
        // センサ情報を取得
        if let Some(interrupt_event) = consumer.dequeue() {
            let id = interrupt_event.id as usize;
            distances[id].append_value(interrupt_event.distance as f32);
        }

        // 走行制御
        match vehicle_state {
            VehicleState::Idle => {
                if let Some(event) = start_event_queue.dequeue() {
                    let diff_back_front = distances[0].get_value() - distances[5].get_value();
                    let rotate = if diff_back_front > 0.0_f32 { 2.0_f32 * PI / 180.0_f32} else { - 2.0_f32 * PI / 180.0_f32};

                    let mut text: String<U40> = String::new();
                    write!(text, "{}, ", diff_back_front).unwrap();
                    println_display(&mut display, text.as_str());

                    if event.pressed {
                        unsafe {
                            let running_system = RUNNING_SYSTEM.as_mut().unwrap();
                            running_system.move_to(vector![0.0_f32, 0.0_f32, rotate]);
                        }
                        vehicle_state = VehicleState::AdjustDir;
                    }
                }
            },
            VehicleState::AdjustDir => {
                if let Some(moved) = wheel_event_queue.dequeue() {
                    moved_count += 1;

                    unsafe {
                        let running_system = RUNNING_SYSTEM.as_mut().unwrap();
                        let vehicle_rotate = Matrix3::new_rotation(vehicle_pose.z);
                        vehicle_pose += vehicle_rotate * running_system.wheel_step_to_vec(&moved);

                        if running_system.on_moved(&moved) {
                            let diff_back_front = distances[0].get_value() - distances[5].get_value();
                            if diff_back_front.abs() < 1.0_f32 {
                                let len = 111.0_f32 + distances[3].get_value() + distances[0].get_value();
                                let diff_beside = distances[3].get_value() - distances[0].get_value();
            
                                let move_len = (diff_beside * 168.0_f32 / len) / 2.0_f32;
                                running_system.move_to(vector![move_len, 0.0_f32, 0.0_f32]);
                                vehicle_state = VehicleState::AdjustCenter;
                            } else {
                                let rotate = if diff_back_front > 0.0_f32 { PI / 180.0_f32} else { - PI / 180.0_f32};
                                running_system.move_to(vector![0.0_f32, 0.0_f32, rotate]);
                            }
                        }
                    }
                }
            },
            VehicleState::AdjustCenter => {
                if let Some(moved) = wheel_event_queue.dequeue() {
                    moved_count += 1;

                    unsafe {
                        let running_system = RUNNING_SYSTEM.as_mut().unwrap();
                        let vehicle_rotate = Matrix3::new_rotation(vehicle_pose.z);
                        vehicle_pose += vehicle_rotate * running_system.wheel_step_to_vec(&moved);

                        if running_system.on_moved(&moved) {
                            let diff_beside = distances[3].get_value() - distances[0].get_value();
                
                            if diff_beside.abs() < 1.5_f32 {
                                running_system.run(vector![0.0_f32, velocity, 0.0_f32]);
                                vehicle_state = VehicleState::Run;
                            } else {
                                let move_len = if diff_beside > 0.0_f32 { 0.5_f32 } else { - 0.5_f32 };
                                running_system.move_to(vector![move_len, 0.0_f32, 0.0_f32]);
                            }
                        }
                    }
                }
            },
            VehicleState::Run => {
                if let Some(moved) = wheel_event_queue.dequeue() {
                    moved_count += 1;

                    if distances[1].get_value() < 40.0_f32 {
                        // 壁が近づいたら
                        if link_index == route.len() - 1 {
                            // ゴールに到着
                            unsafe {
                                let running_system = RUNNING_SYSTEM.as_mut().unwrap();
                                let vehicle_rotate = Matrix3::new_rotation(vehicle_pose.z);
                                vehicle_pose += vehicle_rotate * running_system.wheel_step_to_vec(&moved);
                                running_system.stop();
                            }
                            vehicle_state = VehicleState::Arrive;
                        } else {
                            // 次のリンクを走行開始
                            let current_link = route[link_index];
                            let current_link_vec = (current_link.1 - current_link.0).normalize();
                            let next_link = route[link_index + 1];
                            let next_link_vec = (next_link.1 - next_link.0).normalize();
                            let dot = current_link_vec.dotc(&next_link_vec);
                            let det = current_link_vec.perp(&next_link_vec);
                            let rad = det.atan2(dot);

                            let mut text: String<U40> = String::new();
                            write!(text, "Turn {}, ", rad).unwrap();
                            println_display(&mut display, text.as_str());
        
                            unsafe {
                                let running_system = RUNNING_SYSTEM.as_mut().unwrap();
                                let vehicle_rotate = Matrix3::new_rotation(vehicle_pose.z);
                                vehicle_pose += vehicle_rotate * running_system.wheel_step_to_vec(&moved);
                                running_system.move_to(vector![0.0_f32, 0.0_f32, rad]);
                            }

                            vehicle_state = VehicleState::Turn;
                        }
                    } else if moved_count % 32 == 0 {
                        // 両側の壁の有無に合わせて位置を調整する。
                        let side_wall = calc_side_wall(&maze, &vehicle_pose);

                        // 調整値の計算
                        let bias: f32;
                        let rotate_diff: f32;
                        if side_wall.front_right() == WALL && side_wall.back_right() == WALL 
                                && side_wall.front_left() == WALL && side_wall.back_left() == WALL {
                            // 両側に壁が存在
                            let left_side_distance_sum = distances[0].get_value_inclined() + distances[5].get_value_inclined();
                            let right_side_distance_sum = distances[2].get_value_inclined() + distances[3].get_value_inclined();

                            if left_side_distance_sum - right_side_distance_sum > 5.0_f32 {
                                bias = (left_side_distance_sum - 84.0_f32) / 2.0_f32;
                                rotate_diff = distances[5].get_value_inclined() - distances[0].get_value_inclined();
                            } else if left_side_distance_sum - right_side_distance_sum < -5.0_f32 {
                                bias = - (right_side_distance_sum - 84.0_f32) / 2.0_f32;
                                rotate_diff = - (distances[3].get_value_inclined() - distances[2].get_value_inclined());
                            } else {
                                bias = ((distances[0].get_value_inclined() + distances[5].get_value_inclined()) - (distances[2].get_value_inclined() + distances[3].get_value_inclined())) / 4.0_f32;
                                rotate_diff = (distances[5].get_value_inclined() - distances[0].get_value_inclined() - (distances[3].get_value_inclined() - distances[2].get_value_inclined())) / 2.0_f32;
                            };
                        } else if side_wall.front_right() == WALL && side_wall.back_right() == WALL {
                            // 右側に壁が存在
                            bias = - (distances[2].get_value_inclined() + distances[3].get_value_inclined() - 84.0_f32) / 2.0_f32;
                            rotate_diff = - (distances[3].get_value_inclined() - distances[2].get_value_inclined());
                        } else if side_wall.front_left() == WALL && side_wall.back_left() == WALL {
                            // 左側に壁が存在
                            bias = (distances[0].get_value_inclined() + distances[5].get_value_inclined() - 84.0_f32) / 2.0_f32;
                            rotate_diff = distances[5].get_value_inclined() - distances[0].get_value_inclined();
                        } else {
                            // 両側に壁がない時は位置調整をしない
                            bias = 0.0_f32;
                            rotate_diff = 0.0_f32
                        }
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

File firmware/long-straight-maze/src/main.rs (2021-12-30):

#![no_std]
#![no_main]

use core::f32::consts::{PI, FRAC_PI_2, FRAC_PI_3, FRAC_PI_4, FRAC_PI_6, FRAC_PI_8};
use core::fmt::Write;

use cortex_m::interrupt::free as disable_interrupts;
use cortex_m::peripheral::NVIC;
use heapless::String;
use heapless::consts::{U8, U16, U40};
use heapless::spsc::Queue;
use micromath::F32Ext;
use vl53l0x::VL53L0x;
use xca9548a::{I2cSlave, SlaveAddr, Xca9548a};

use panic_halt as _;

use embedded_graphics::mono_font::{ascii::FONT_10X20, MonoTextStyle};
use embedded_graphics::pixelcolor::Rgb565;
use embedded_graphics::prelude::*;
use embedded_graphics::primitives::{Rectangle, PrimitiveStyle};
use embedded_graphics::text::Text;

use nalgebra as na;
use na::{Matrix3, Vector3, matrix, vector};
use na::base::SVector;

use wio::hal::eic::ConfigurableEIC;
use wio_terminal as wio;
use wio::{entry, Display, Pins};
use wio::hal::clock::GenericClockController;
use wio::hal::delay::Delay;
use wio::hal::common::eic;
use wio::hal::common::eic::pin::{ExtInt4, ExtInt6, ExtInt7, ExtInt10, ExtInt12, ExtInt13, ExtInt14, ExternalInterrupt, Sense};
use wio::hal::gpio;
use wio::hal::gpio::v1::{Port, Pa4, Pa16, Pa17, Pa6, Pb7, Pb12, Pb13, Pb14, Pc26, PfD};
use wio::hal::gpio::v2::{Alternate, D, Floating, Input, Interrupt, Output, PA07, PA16, PA17, PB04, PB05, PB06, PB08, PB09, Pin, PinId, PushPull};
use wio::hal::sercom::v2::{Pad0, Pad1};
use wio::hal::sercom::Pad;
use wio::hal::sercom::{I2CMaster3, PadPin, Sercom3Pad0, Sercom3Pad1};
use wio::hal::timer::{Count16, TimerCounter};
use wio::pac::{CorePeripherals, Peripherals, SERCOM3, TC2, TC3, TC4, interrupt};
use wio::prelude::*;

/* 
 * 走行装置系
 */
#[derive(Clone, Copy)]
enum WheelRotateDirection {
    ClockWise,
    CounterClockWise,
}

struct Wheel<S: PinId, D: PinId, T: Count16> {
    id: u32,
    direction: WheelRotateDirection,
    step_pin: Pin<S, Output<PushPull>>,
    direction_pin: Pin<D, Output<PushPull>>,
    timer_counter: TimerCounter<T>,
    radius: f32,
}

impl<S: PinId, D: PinId, T: Count16> Wheel<S, D, T> {
    const RADIUS: f32 = 24.0_f32;

    fn new(id: u32, step_pin: Pin<S, Input<Floating>>, direction_pin: Pin<D, Input<Floating>>,
        timer_counter: TimerCounter<T>, interrupt: interrupt) -> Wheel<S, D, T>{
            let mut wheel = Wheel {
                id,
                direction: WheelRotateDirection::ClockWise,
                step_pin: step_pin.into_push_pull_output(),
                direction_pin: direction_pin.into_push_pull_output(),
                timer_counter,
                radius: Self::RADIUS,
            };
            wheel.set_rotate_direction(WheelRotateDirection::ClockWise);

            unsafe {
                NVIC::unmask(interrupt);
            }

            wheel
    }

    fn step(&mut self) {
        self.step_pin.toggle().unwrap();
    }

    fn set_rotate_direction(&mut self, dir: WheelRotateDirection) {
        self.direction = dir;
        match dir {
            WheelRotateDirection::ClockWise => {
                self.direction_pin.set_high().unwrap();
            },
            WheelRotateDirection::CounterClockWise => {
                self.direction_pin.set_low().unwrap();
            }
        }
    }

    fn start_with_rps(&mut self, rotate_per_sec: f32) {
        if rotate_per_sec < 0_f32 {
            self.direction = WheelRotateDirection::CounterClockWise;
            self.set_rotate_direction(WheelRotateDirection::CounterClockWise)
        } else {
            self.direction = WheelRotateDirection::ClockWise;
            self.set_rotate_direction(WheelRotateDirection::ClockWise)
        }
        let pulse_hz = ((2_f32 * 200_f32 * rotate_per_sec.abs()) as u32).hz();
        self.timer_counter.start(pulse_hz);
        self.timer_counter.enable_interrupt();
    }

    fn start_with_speed(&mut self, speed_mm_per_sec: f32) {
        if -0.1_f32< speed_mm_per_sec && speed_mm_per_sec < 0.1 {
            self.stop();
        } else {
            self.start_with_rps(speed_mm_per_sec / (2.0_f32 * PI * self.radius));
        }
    }

    fn stop(&mut self) {
        self.timer_counter.disable_interrupt();
    }
}

macro_rules! wheel_interrupt {
    ($RunningSystem:ident, $Handler:ident, $Wheel:ident) => {
        #[interrupt]
        fn $Handler() {
            disable_interrupts(|_cs| unsafe {
                let running_system = $RunningSystem.as_mut().unwrap();
                running_system.$Wheel.step();
                running_system.$Wheel.timer_counter.wait().unwrap();

                let mut q = WHEEL_MOVED_EVENT_QUEUE.split().0;
                let distance = {
                    match running_system.$Wheel.direction {
                        WheelRotateDirection::ClockWise => {
                            (2.0_f32 * PI * running_system.$Wheel.radius) / (2.0_f32 * 200.0_f32)
                        },
                        WheelRotateDirection::CounterClockWise => {
                            (- 2.0_f32 * PI * running_system.$Wheel.radius) / (2.0_f32 * 200.0_f32)
                        }
                    }
                };
                q.enqueue(WheelMovedEvent {
                    id: running_system.$Wheel.id,
                    distance: distance
                }).ok();
            });
        }
    };
}

struct WheelMovedEvent {
    id: u32,
    distance: f32,
}

struct RunningSystem<S0: PinId, D0: PinId, T0: Count16, 
        S1: PinId, D1: PinId, T1: Count16, S2: PinId, D2: PinId, T2: Count16> {
    wheel_0: Wheel<S0, D0, T0>,
    wheel_1: Wheel<S1, D1, T1>,
    wheel_2: Wheel<S2, D2, T2>,
    mat_for_wheel_v: Matrix3<f32>,
    mat_for_odometry: Matrix3<f32>,
}
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

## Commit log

2021-07-29 内蔵LEDでLチカ
2021-07-29 READMEを作成
2021-07-29 LICENSEファイルを作成
2021-07-29 ピンヘッダにLEDを繋いでLチカする
2021-07-30 内蔵LチカのREADMEを記述
2021-07-30 ブレッド・ボードでLチカ
    [Schematic.fzz]
2021-07-30 開発環境の構築方法について記述
2021-07-30 参考情報のURLを追加
2021-07-30 開発記録表を作成
2021-07-30 開発記録表が表になっていないのを修正
2021-08-11 参考情報のRustDocを追加
2021-08-11 ステッピングモータのSPIの初期化コードを実装
2021-08-14 接続図を作成
    [stepper_motor_breadboard.fzz]
2021-08-14 SPIのクロック周波数を変更
2021-08-14 L6470を使ってステッピングモータを回転させる
2021-08-14 ステッピングモータのREADMEを修正
2021-08-15 外部LED接続図のWio Terminalをカスタム部品に変更
    [Schematic.fzz]
2021-08-15 ステッピングモータをステップ数指定で制御
    [stepper_motor_breadboard.fzz]
2021-08-17 ディスプレイ名を修正。READMEのリンクを修正
    [stepper_motor_breadboard.fzz]
2021-08-29 内部と外部のLEDの点灯を制御
    [Schematic.fzz]
2021-08-29 LEDの構造体をジェネリック化
2021-08-29 13番ピンを割込み用のピンに設定
2021-09-05 割込み処理の関数を追加
2021-09-05 ボタンの操作を割込みで処理して内蔵LEDのOn/Offを制御する
2021-09-05 ボタン操作の割込みのボタンを1つに絞る
2021-09-07 外部ピンの割込みのコードを一旦削除
    [Schematic.fzz]
2021-09-09 ヘッダ・ピンから割込みをかける
    [button_external.fzz]
2021-09-09 READMEのステップを追加
2021-09-11 Third party Licenseのファイルを移動
2021-09-11 ステッピングモータの回転の完了を割込みで受け取る
    [stepper_motor_breadboard.fzz]
2021-09-12 ボタンから割込みピンへ名前を変更
2021-09-12 ボタンから割込みピンへ名前を変更(その2)
2021-09-12 ステッピングモータの動作完了の割込み処理へのリンクを作成
2021-09-13 内蔵ブザーを鳴らす
2021-09-19 ステッピングモータをステップクロック・モードで動かす
    [stepper_motor_breadboard.fzz]
2021-10-02 A4988モータドライバでステッピングモータを駆動
    [stepper_motor_breadboard.fzz]
2021-10-09 ステッピングモータを3つ接続
    [stepper_motor_breadboard.fzz]
2021-10-10 3つのステッピングモータを別々の速度で回転させる
    [stepper_motor_breadboard.fzz]
2021-10-10 TopのREADMEに進捗を反映
2021-10-10 リファクタリング
2021-10-13 筐体試作 その1
    [core1_3_motor-Body.stl, core1_3_motor.FCStd]
2021-10-13 3Dプリンタ用のデータは削除
2021-10-16 筐体試作 その2
    [core1_3_motor_2-Body.stl, core1_3_motor_2.FCStd]
2021-10-17 筐体試作 その3
    [core1_3_motor_3-Body.stl, core1_3_motor_3.FCStd]
2021-10-17 筐体試作 マイコン部分
    [core2-Body.stl, core2.FCStd]
2021-10-17 試作1号機の写真を追加
2021-10-18 試作1号機で往復運動
2021-10-18 動画を変更
2021-10-19 筐体上部改良
    [core2_2-Body.stl, core2_2.FCStd]
2021-10-20 往復運動をタイマー割込みで
    [stepper_motor_breadboard.fzz]
2021-10-20 READMEを更新
2021-10-20 READMEの筐体の写真を動画に変更
2021-10-22 リファクタリング。Wheelクラスを作成
    [stepper_motor_breadboard.fzz]
2021-10-23 リファクタリング。車輪とタイマー・コントローラの対応を修正。
2021-10-23 超信地旋回をする
2021-10-23 車輪の初期化をリファクタリング。
2021-10-24 更にリファクタリング
2021-10-24 車輪のリファクタリングを一旦完了
2021-10-24 リファクタリング。車輪関連の型名
2021-10-24 リファクタリング: 車輪にIDを追加
2021-10-24 リファクタリング。gpio::v2に切り替え
2021-10-24 超信地旋回で定期的に逆回転させる
2021-10-24 多重割込みを禁止する
2021-10-27 車輪の制御コマンドを作成
2021-10-28 トップのREADMEのリンクを修正
2021-10-29 三角形の動きのコーディング
    バグがあり想定通りは動かない。
2021-10-30 I2Cを使うためGPIOをv1に戻す
2021-10-30 UARTを使えるようにする
2021-10-30 三角形の動きを実装
2021-10-31 三角運動のREADMEやブレッドボードの図を記述
    [stepper_motor_breadboard.fzz]
2021-10-31 ブレッドボードのPNGの図を作成
2021-10-31 三角運動へのリンクを修正
2021-10-31 加速運動のプロジェクト作成
    [stepper_motor_breadboard.fzz]
2021-10-31 現在のタイマーのタイムアウトを保持
2021-11-03 タイマーコントローラーのタイムアウトを変更しようとする
    上手くいかない。
2021-11-03 TCCのプロジェクトを作成。ブザーをPWMを直接使って鳴らす。
    [stepper_motor_breadboard.fzz]
2021-11-03 加速運動をする
2021-11-03 加速運動のREADMEを更新
2021-11-06 UARTをSetsを使わずにPinsから生成させる
    [stepper_motor_breadboard.fzz]
2021-11-06 ヘッダ・ピンでI2Cを生成
2021-11-06 TOFセンサで距離を計測
2021-11-06 TOFセンサで測定のブレッドボードの図を作成し、READMEを修正
    [breadboard.fzz, stepper_motor_breadboard.fzz]
2021-11-06 トップページのREADMEにTOFセンサへのリンクを追加
2021-11-07 筐体(その2)の画像のサイズを調整
2021-11-07 筐体1にセンサマウントを追加
    [core1_motor_sensor-Body.stl, core1_motor_sensor.FCStd]
2021-11-07 VL53L0Xの使い方について記述
2021-11-17 オムニホイールのハブを設計
    [omni_wheel_hub-Body.stl, omni_wheel_hub.FCStd]
2021-11-17 TOF距離センサを搭載
    [core1_motor_sensor_2-Body.stl, core1_motor_sensor_2.FCStd, core1_motor_sensor_3-Body.stl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]
2021-11-21 TOFセンサのマウント部分を変更し、わずかに小型化
    [core1_motor_sensor_4-Body.stl, core1_motor_sensor_4.FCStd]
2021-11-21 I2Cマルチプレクサを使用してTOFセンサを2個つなげる
    [breadboard.fzz]
2021-11-21 I2Cハブの接続図を作成
    [breadboard.fzz]
2021-11-23 TOFセンサを6個接続
    [breadboard.fzz]
2021-11-23 TOFセンサを配列化
2021-11-23 LCDに文字表示
    [breadboard.fzz]
2021-11-23 TOFセンサを動かしながらLCDに文字表示
2021-11-23 TOFの測定値をformatを使って出力
2021-11-23 TOFの測定値をUARTとLCDに出力
2021-11-23 不要なuseを削除
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2021-11-23 TOF6つの接続図を作成
    [breadboard.fzz]
2021-11-23 TOF6つのREADMEを修正
2021-11-25 迷路のパーツを設計
    [maze_pillar-Body.stl, maze_pillar.FCStd, maze_wall_cap-Body.stl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]
2021-11-28 筐体上部の設計見直し、I2Cハブを搭載
    [core2_3-Body.stl, core2_3.FCStd]
2021-11-28 筐体上部のI2Cハブの固定部を改善
    [core2_3-Body.stl, core2_3.FCStd]
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2021-12-04 TOFセンサを1つ使って連続測定モードで測定
    [breadboard.fzz]
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2021-12-04 I2Cハブで割込みで測定
    [breadboard.fzz]
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2021-12-11 バッテーリーシャーシの電源ボタンを押せるように筐体上部を変更
    [core2_3-Body.stl, core2_3.FCStd]
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2021-12-18 EICを共有できるように修正
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2021-12-19 直線迷路: リファクタリング(TOFセンサのイベントのIDを修正)
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2021-12-26 筐体上部をバッテリーボタンを押しやすいように変更
    [core2_3-Body.stl, core2_3.FCStd]
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2021-12-27 センサの入力の指数平滑平均を取る
    [breadboard.fzz]
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2021-12-29 長い直線迷路: 自車の旋回を修正
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2021-12-30 READMEを修正・更新
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2022-01-08 長い直線迷路のディレクトリ名のタイポを修正
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2022-01-09 4マス迷路: 初期位置調整に失敗するのを修正
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2022-01-10 迷路パーツ: T字とI字のキャップを作成
    [maze_wall_cap_I-Body.stl, maze_wall_cap_I.FCStd, maze_wall_cap_T-Body001.stl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]
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2022-01-11 渦巻き迷路: ルートデータを作成。
    原点と座標系を変更。それに伴い旋回角の計算式を修正
2022-01-11 渦巻き迷路: 旋回角の計算のバグを修正
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2022-01-13 渦巻き迷路: 直進性を改善。途中で止まるのを修正
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2022-01-15 渦巻き迷路: 初期位置調整のバグを修正
2022-01-15 渦巻き迷路: ホイール方向の移動の補正式のバグを修正
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2022-01-22 地図描画: 画像の表示サイズを修正
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2022-01-22 現在地表示: 動画を追加 close #7
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2022-01-25 周辺壁表示: 現在地表示のバグ修正
2022-01-25 周辺壁表示: 旋回時に止まってしまうのを修正
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2022-01-28 Revert "周辺壁表示: 不要なコードを削除"
    This reverts commit 94fe20d667b9bd8663620a168aa9fc161c888655.
    [main.rs]
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2022-01-30 側面壁表示: Viewのクリア処理バグ修正。自車の向きのバグ修正
    まだ、東向きの時の表示がおかしい。走行時のセルの位置が想定外になる
2022-01-30 側面壁表示: 東西進行時の表示のバグを修正
2022-01-30 自車のpose表示の画面乱れを修正
2022-01-30 側面壁表示: マス目の境目付近でも表示できるようにする。 close #8
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2022-01-30 センサ移動平均: 方向修正の頻度を上げる
    直進性が安定している
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2022-01-31 センサ移動平均: 区間数3で移動平均をとる #9
    指数移動平均とあまり差はないかも。
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2022-02-03 両側センサ: 両側の壁のセンサの測定値を使って位置調整 #11
    未テスト
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2022-02-04 両側センサ: 暫定実装完了 #11
    バグあり。暴走する。
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2022-02-05 センサ指数平滑平均: グラフ表示の誤記を修正
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2023-01-02 TOFセンサの配置変更のCADデータ
    [core1_motor_tof_9axis-Body.stl, core1_motor_tof_9axis.FCStd]
2023-01-07 9軸センサの接続。プルアップ抵抗が必要
    [breadboard.fzz]
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2023-01-07 ブレッドボードの図を修正
    [breadboard.fzz]
2023-01-07 9軸センサ: プルアップ抵抗を図に追加
    [breadboard.fzz]
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2023-01-25 I2CバスにTOFセンサと9軸センサを接続
    [breadboard.fzz]
2023-01-25 筐体設計を見直し
    [core1_motor_sensor_5-Body.stl, core1_motor_sensor_5.FCStd, core2_4-Body.stl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]
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
